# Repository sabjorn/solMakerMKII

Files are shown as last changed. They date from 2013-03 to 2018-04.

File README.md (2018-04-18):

## Sol(enoid)MakerMarkII
### About
Included in this package is all (I hope) the necessary components to build a copy of the Sol-MakerMKII solenoid control 'robot'.

This device was designed as a shield for an Arduino Uno R3 and you will, therefore, need to get one if you don't already have it. The circuit size (and cost) could be easily reduced by scaling the whole circuit to fit an Arduino Mini (the code should be cross compatible).

The basic principle of the device is this: electrical power is input into the device. This power is gated by twelve transistors which are closed. Each transistor is an output for a device which operates with applied electrical current (solenoids, for example). These transistor gates are controlled by the 12 digital output pins from the Ardunio Uno. By sending a signal to the Arduino, via the serial bus, the Arduino is able to open any/all of these transistor gates. Thus, if you attach a solenoid (electro-mechanical piston) to a gate, and open it with the Arduino, you can send electricity to the device and cause it to move.

Solenoids are not the only device for which this circuit will work. Anything which operated using a DC power supply (which matches the input voltage from your selected power supply) can be controlled. Example: Electric motors from tape machines.

**CAUTION**: This device will operate without issue if nothing is connected to the outputs. BUT if the outputs from the transistors are crossed, THE TRANSISTORS WILL BLOW UP. Furthermore, if the power supply voltage polarity is switched (+ and ground switched) THE TRANSISTORS WILL (also) BLOW UP. It would be a good idea to attach a diode to the power supply input to prevent this from happening by mistake.

The LEDs on this device act as indicators of the Arduino pins' activity. They will operate without the external power supply connected. They are helpful for troubleshooting connection problems and have the added benefit of looking very cool.
 
Included in this package:
	
	* Fritzing and Gerber file for PCB ('solMakerMKII_circuit' directory).

	* Code for the Arduino and a Max/MSP patch to allow direct use of MIDI 
	devices ('solMakerMKII_code' directory).

	* Diagrams ('solMakerMKII_diagrams' directory).
	
	* More elaborate documentation (.pdf file and the latex files needed to
	edit it; 'solMakerMKII_documentation' directory).

For contribution ideas, please check the .pdf documentation. There is a list at the end of the document. 

### Development Status
This project is effectively deprecated. The code will be ported to be used as part of another project--[dreamIO](https://github.com/sabjorn/dreamio). This will allow for control of solenoids over WiFi using OSC.

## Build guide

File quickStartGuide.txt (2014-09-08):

Quick Start Guide

1) Order PCB. The 'solMakerMKII_circuit' directory contains all the files for this. The Gerber directory contains the exported circuit (gerber files) created using Fritzing (open source PCB design software).

2) Assemble board. The 'solMakerMKII_diagrams' directory contains the specs for all the required components. A DC power supply will be required (voltage and maximum current will depend on the items being controlled by the circuit). Solenoids, or other DC powered items, will need to be found. The type of connectors used to attach the power supply and solenoids to the PCB will also be determened based on the context of the situationâ any type of connector you choose should work.

3) Flash the Arduino. The 'solMakerMKII_code' directory contains a directory called 'solMakerMKII' which houses the Arduino's code. The PCB is designed for an Arduino Uno and, with standard headers, should attach easily to the back of the board.

4) Open 'sol-MakerMKIIControl.maxpat'. This file is contained in the 'solMakerMKII_code' directory. It acts as a midi decoder. If you do not have Max/MSP, a free runtime can be download which will allow you to use the patch. Make sure the Arduino is connected, and recognized by your computer, via USB AND that no other task (i.e. Arduino serial window) is reading the Arduino's serial messages. Once the maxpatch is opened, the midi input can be changed to receive from any midi device or software (i.e. Ableton live). The Arduino code accepts midi notes 60 (C3) to 71 (B3) (inclusive) with standard velocity values when coupled with the maxpatch. If you have issue connecting to the Arduino with the patch, the Serial object may not be connecting to the right port.

5) Have fun.

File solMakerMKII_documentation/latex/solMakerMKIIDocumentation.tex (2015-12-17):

% $Id: AllegProposal.tex,v 1.8 2000/07/05 21:02:12 culver Exp $
% AllegProposal.tex
% by A. Thall
% 13. Feb 2003
%
% Small edits and a few additions made by R. Roos
% 21 Jan 2007
% Most particularly, the "box" around the thesis statement has been removed,
% section titles have been modified. The section named "Prior work II" has
% been commented out. The \topmargin has been changed to -.5in and the
% change to \parindent has been commented out.
% The filename "nausicaa.eps" has been changed to simply "nausicaa" so that
% pdflatex can be used on the file (and a file named "nausicaa.pdf" has
% been created using the "epstopdf" command).
% Several subsections have been added to illustrate subsection usage.
% The word "comp" has been replaced by "project" or "thesis" throughout.
% Other small changes have been made.
%
% This document provides a sample Senior Project Proposal template for use
% by students in Allegheny's CS and Applied Computing programs.

\NeedsTeXFormat{LaTeX2e}
\documentclass[12pt]{article}

%The following is used by WinEdt to set up cross-referencing to the BibTeX files
%It is NOT commented out---the comment lets it be simply ignored by non-WinEdt LaTeX compilers

%GATHER{mybibtexDB.bib}

\usepackage{setspace}
\usepackage{amsmath}
\usepackage{amssymb}
\usepackage{epsfig}
\usepackage{fancybox}
\usepackage{listings}
\usepackage{algo}
\usepackage{url}
\usepackage{hyperref}

% for watermakr
\usepackage{graphicx}
%\usepackage{tikz}
%\usepackage{eso-pic}

%\newcommand\BackgroundPicA{\put(-50,50){{
%\begin{tikzpicture}\node[opacity=0.15]{
%\includegraphics[scale=5.0]{test.png}};
%\end{tikzpicture}%
%}}}

%\makeatletter
%\AddToShipoutPicture{\BackgroundPicA}
%\makeatother

\setlength{\textheight}{9in}
\setlength{\textwidth}{6in}
\setlength{\oddsidemargin}{.25in}
\setlength{\topmargin}{-.5in}  % changed from -.25 by RSR on 1/21/07
%\parindent .5in    % commented out by RSR 1/21/07

%put words in the hyphenation statement if you want to enforce
%how LaTeX should break them (or not) at the end of a line.
%\hyphenation{repre-sen-tations problems exact linear}
\hyphenation{itself}

%%%%%
%% Commented out -- RSR, 1/21/07
%%%%%
% The following provides a box to surround the thesis statement
%\newenvironment{Thesis}%
%{\begin{Sbox}\begin{minipage}{.95\linewidth}}%
%{\end{minipage}\end{Sbox}\begin{center}\fbox{\TheSbox}\end{center}}

\title{Sol-MakerMKII: Arduino Uno Based Solenoid Controller}
\author{Steven A. Bj\o rnson}

\begin{document}

% You can specify a language and other options for
% the code-formatting "listings" package
\lstset{language=C++,basicstyle=\small,
        stringstyle=\ttfamily,showstringspaces=false}

\singlespace
\maketitle

\doublespace
% This sets section-numbering to only include Section and Subsection numbers
\setcounter{secnumdepth}{2}

\section{Outline:}\label{ch:overview}

The Sol-Maker MKII is a shield designed for the Arduino Uno. This shield allows for individual control of up to twelve solenoids (push, pull, or rotary) utilizing an external power supply; 12 or 24 volts depending on the power requirements of the solenoids. Control of each solenoid is made possible by communication with each of the 12 output pins on the Arduino UnoÐ1 pin per solenoid. The current code compiled on the Ardiuino allows the user to send messages on/off messages from a computer to the Arduino via the USB port.

\section{Circuit:}
The design of the circuit is quite simple. Each of the 12 digital outputs of the Arduino Uno (outputs 2 to 13) are connected to identical modules. Each module contains a resistor, a TIP120 transistor, and a diode. These modules allow the shared voltage (12 or 24 volt external power supply) to be controlled by the digital output of the Arduino for each solenoid.

	In each module the TIP120 acts as a gate which is opened and closed by the 5 volt output from the digital output pins of the Arduino. The resistor is necessary since the TIP120  provides very low impedance and so without it the Arduino could be damaged. 

		A diode is run in parallel with each solenoid. This is necessary because solenoids are inductors and after a solenoid is cycled (charged and released) the plunger returns to the starting point (by way of mechanical potential energy; a spring or gravity will return the plunger to home). This returning plunger pushes current the opposite direction in the circuit and thus without the diode this reversed current could potentially damage the transistor.

	The second section of each module contains a resistor and an light emitting diode (LED). This section is connected in parallel to each of the digital output pins which control the solenoids. When a solenoid is activated, a corresponding LED is activated. The LEDs are powered by the 5V provided by the digital outputs and do not utilize the external power supply. 

		A resistor in series with the LED provides the same function as the TIP120's resistor. 

		The purpose of the LED is to provide visual feedback and, since it will continue to operate when the external power supply is not on and when a solenoid is not connected, it notifies the user which module is being activated. This is advantageous for fault checking during system setup (i.e. finding out which output you are controlling before plugging a solenoid into that modules output).

\subsection{Solenoids:}
\begin{itemize}
\item Sol1 through Sol12 - GUARDIAN ELECTRIC TP6X12-I-24D 24V Solenoids.
\end{itemize}

Any solenoid with a voltage range of 12 to 24 volts should work with this circuit. There is a possibility of damaging a solenoid by holding current for too long if it is not designed to hold for long periods of time.\footnote{Remember that the input power supply voltage must match the requirement of your solenoids and that your power supply should have a maximum current rating to allow all the solenoids to fire at once. For example, since GUARDIAN ELECTRIC TP6X12-I-24D  solenoids require  24V and 198mA each, the power supply must produce 24V and be capable of producing a current of 2376mA.}

\subsection{Resistor Values:}
\begin{itemize}
\item R1 through R12 - 2.2 kOhm.
\item LED-R1 through LED-R12 - 100 Ohm.
\end{itemize}

\subsection{Diodes:}
\begin{itemize}
\item D1 through D12 - 1N4001 or other suitable diode.
\end{itemize}

\subsection{LEDs:}
\begin{itemize}
\item LED1 through LED12 - any colour; 5mm;\footnote{Resistors LED-R1 through LED-R12 are calculated based on 3.3Vf and 20mA. Thus, if an LED with a different Vf is used a change of it's corresponding resistor is required. The resistance of LED-R1 through LED-R12 was set higher than required in the hopes of preventing any issue problem when using different colour LEDs.}
\end{itemize}

\section{Control:}
Control is possible utilizing the USB port on the Arduino. The code (outline below) allows the user to send an on/off byte to each solenoid individually by coupling the byte with an address. Thus, although Max/MSP has been utilized for control, any programming language or software can be used as long as it follows serial message format.

\section{Dynamics:}
Originally \emph{pulse width modulation} (PWM) was used for all supported pins with the belief that control of the output voltage would be useful for the dynamic capability of the solenoids. This was unfortunate because the Arduino Uno only supports 6 pins for PWM. It became apparent, however, that PWM was unnecessary since the velocity of the solenoids can be effectively controlled with the hold-time--the length of time that current is pushed through a solenoid. Thus, if a solenoid is given current for 10ms it will hit with less force than if current is held for 20ms. Each solenoid is likely to have idiosyncrasies and thus a method of calibration would be useful\footnote{A microphone is likely a requirement for such an operation. I.e.  A microphone would have to be placed near the device and it's sound energy output measured at various stages (5ms, 10ms, 20ms, etc). Once the sound energy hit it's maximum (maximum dB), the maximum current holding value is found. Each solenoid would have to undergo this process and it would depend greatly on the distance from the object being struck. If the solenoid was to be moved in any way, it would likely have to be re-calibrated. Furthermore, this calibration process could be used to create a table for midi value scaling. Nonetheless, this can all be done by ear, although not with optimum effect} but a simple scaling of MIDI velocity (0 - 127) with a range of 5 - 100ms should suffice.

\section{Future Improvements:}
\begin{itemize}
\item A multiplexer could be used to increase number of solenoids. An alternative would be to use an 	Arduino Mega which supports a larger number of digital output pins. 
\item Since the shield obscures the Arduino completely a serial send/receive light on the board would be useful.
\item  With an Arduino network adapter shield the system could easily utilize Open Sound Control (OSC) making the whole system more user friendly. Otherwise a simple MIDI input port would be sufficient for greater usability.
\item To reduce the cost of manufacturing, the circuit could be redesigned to fit an Arduino Mini.
\item To prevent accidentally plugging the power supply in with the polarity reversed, the circuit could be redesigned to include a diode at the power input. 
\end{itemize}

\end{document}

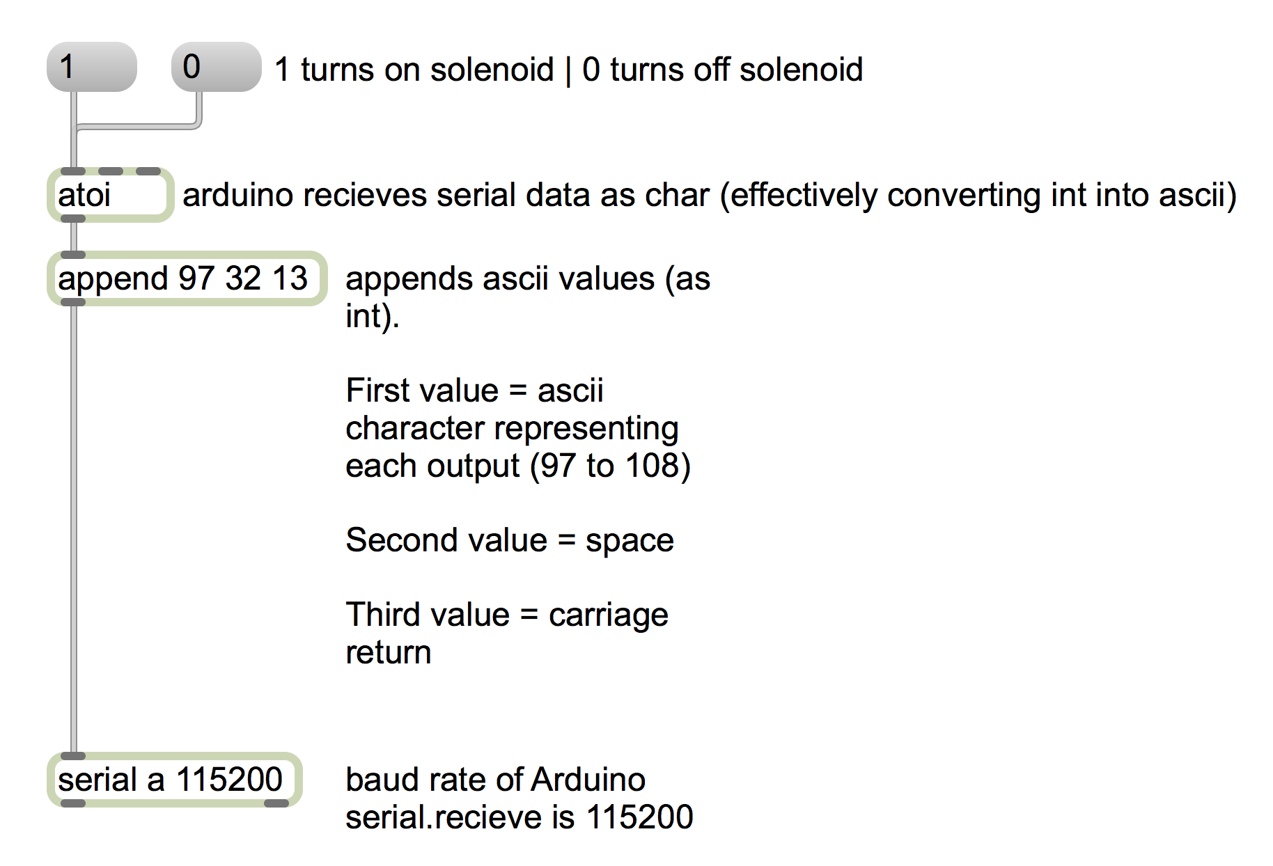
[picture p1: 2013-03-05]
solMakerMKII_documentation/images/sol-makerSimpleExample.png

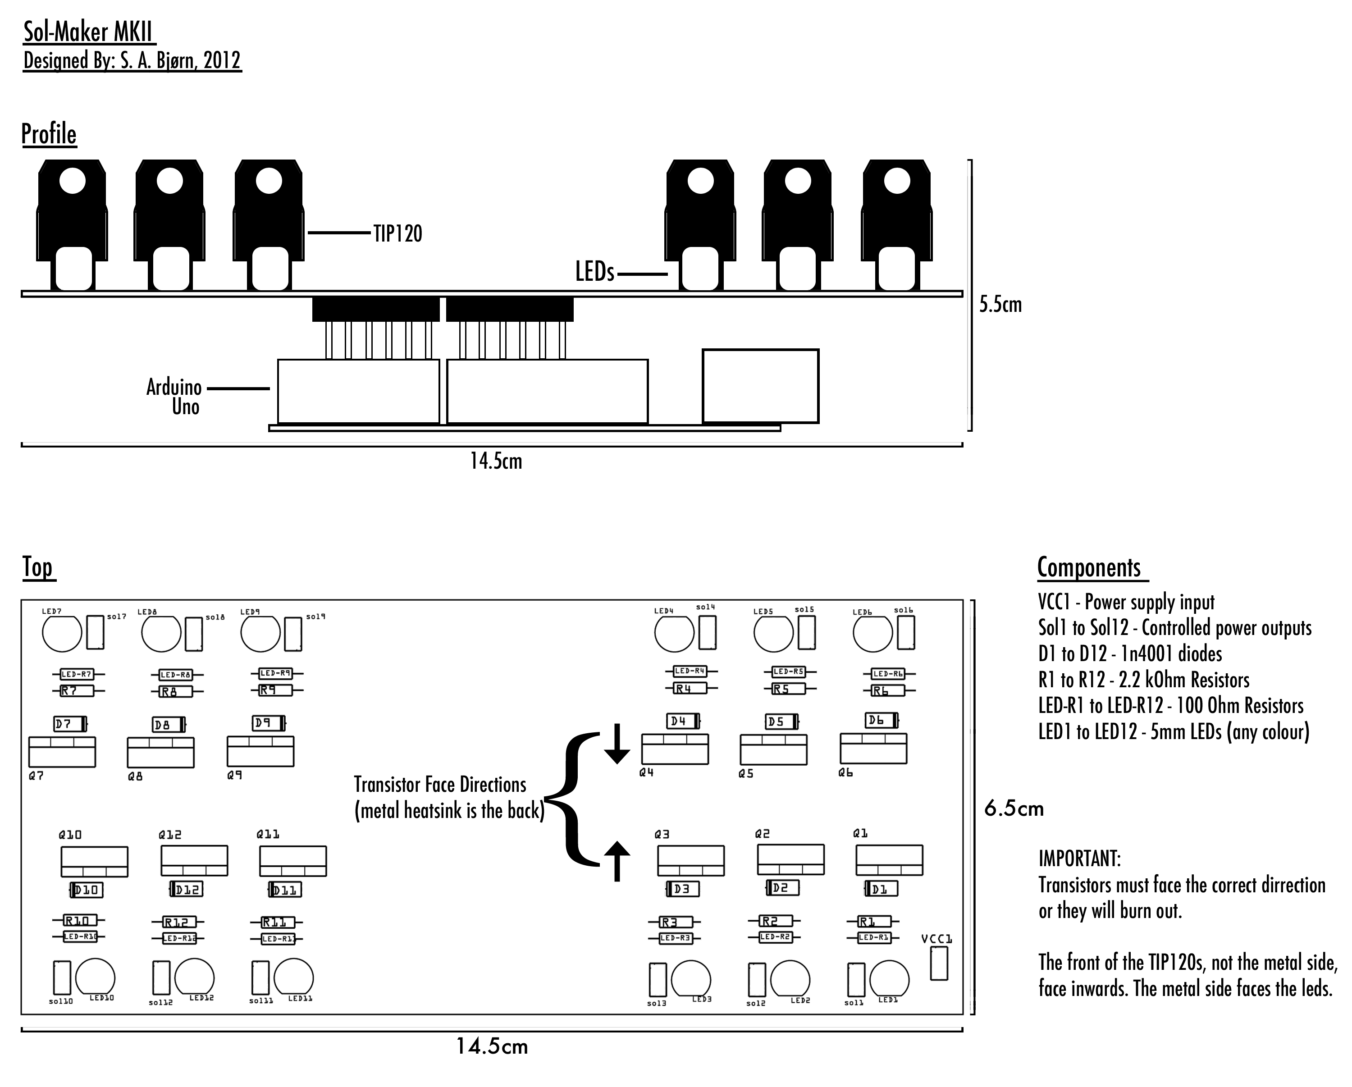
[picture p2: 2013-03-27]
solMakerMKII_diagrams/solMakerMKII-diagram.png

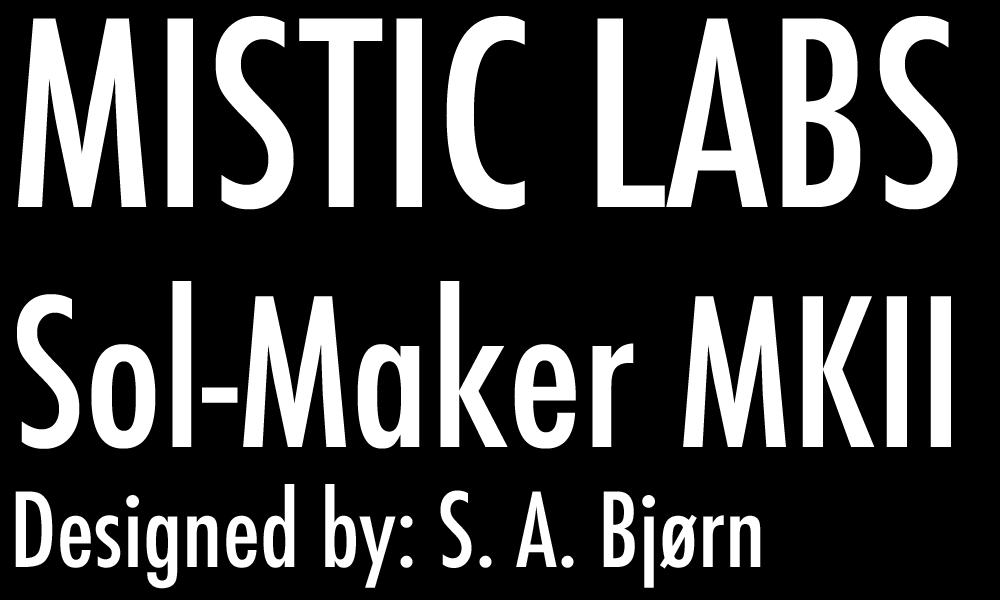
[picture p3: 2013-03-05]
solMakerMKII_circuit/fritzing/mistic2.gif

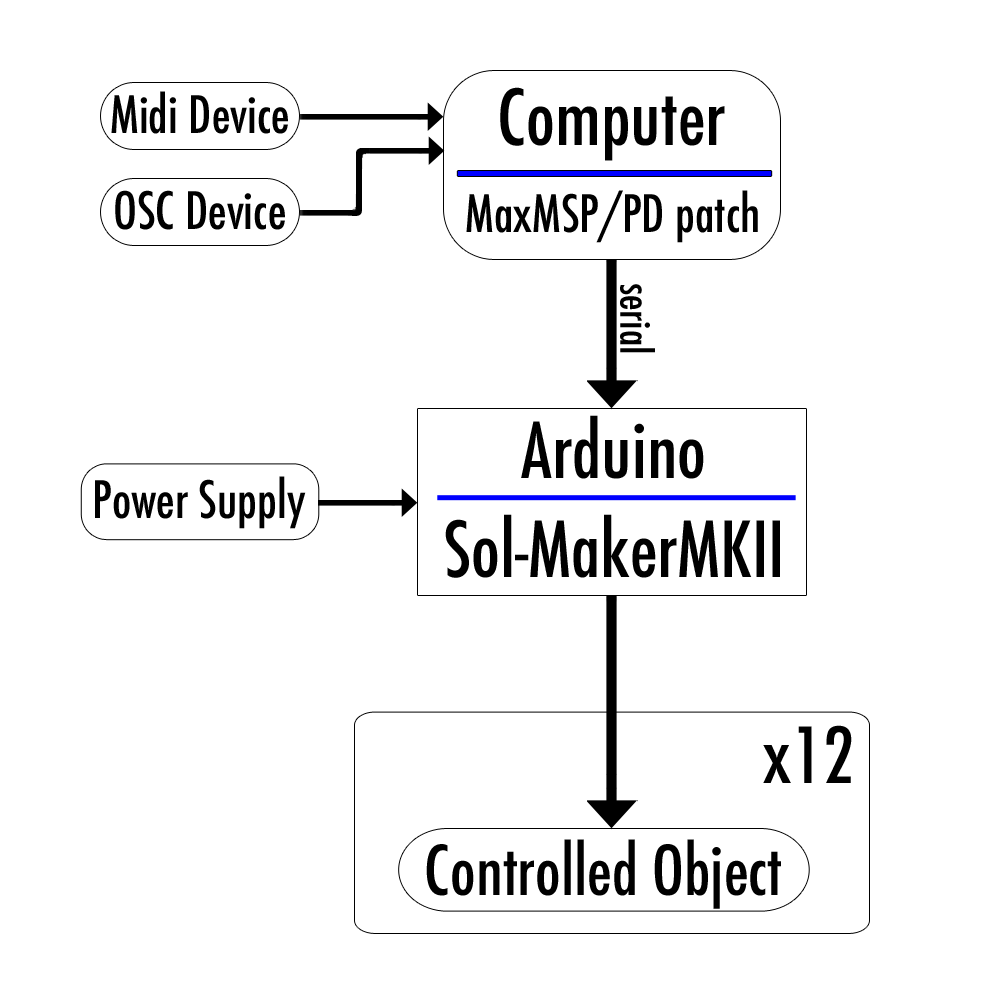
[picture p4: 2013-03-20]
solMakerMKII_diagrams/solMakerMKII-systemDiagram.png

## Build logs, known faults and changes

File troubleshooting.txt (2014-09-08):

Troubleshooting Guide:

LEDs:
The circuit is designed so that even if there is no external power, the Arduino's power will still light up the LEDs when it receives a valid message. The circuit was designed like this to enable the user to quickly troubleshoot problems.

If LEDs do not operate, check to make sure that the serial receive ('rx') light is operating on the Arduino when a signal is sent via USB. If no message is being sent, try changing the serial port in the solMakerMKIIMidiControl.maxpat (patch can be edited using text editor. The Serial object is set to port 'a', try ports 'b', 'c', etc). If the Arduino software serial monitor window is open, the maxpatch will not work.

If the Arduino's serial receive light is operating there may be a problem with the connection between the Arduino and the board or there may be issues with the soldering, or the installation, of components (specifically LED-R1 through LED-R12 and LED1 through LED12).

Not Current Output:

If the LEDs are working and there is no current coming out of the board (sol1 through sol12) then the power supply connection should be checked first. If the power supply is connected properly and operating normally, the TIP120 transistors may be wired backwards (although this is not likely the case because a revered current will usually cause the transistors to burn out) or may not have a solid connection. The resistors attached to the TIP120s (R1 through R12) may also have poor connections. 

It is unclear what may happen if the diodes (D1 through D12) are connected backwards. The TIP120 transistors are likely to be damaged.

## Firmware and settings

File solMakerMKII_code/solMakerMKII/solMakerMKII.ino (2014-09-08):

/*
solMakerMKII
Copyright September 2014, Steven A. Bjornson

Based on code by Chris Vecchio, 2010 (http://www.noisemantra.com/Physical%20Computing/arduino-MaxMSP%20communications%2011.pdf).

Distributed under the terms of the GNU General Public License.

This file is part of SolMakerMKII, an open source solenoid control system.

SolMakerMII is free software (and hardware): you can redistribute it and/or modify it under the terms of the GNU General Public License as published by the Free Software Foundation, either version 3 of the License, or (at your option) any later version.

SolMakerMKII is distributed in the hope that it will be useful, but WITHOUT ANY WARRANTY; without even the implied warranty of MERCHANTABILITY or FITNESS FOR A PARTICULAR PURPOSE.  

See the GNU General Public License for more details.

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
This code will allow user to send data to Arduino over USB to active 12 of the digital output pins. 
When connected to the solMakerMKII board, these 12 outputs will control the flow of an external power supply in order to turn ON and OFF solenoids.
*/

// used to set the OFF state of arduino pin output register
uint8_t out_mask[8] = 
{
	B00000001,
	B00000010,
	B00000100,
	B00001000,
	B00010000,
	B00100000,
	B01000000,
	B10000000
};
// used to set the OFF state of arduino pin output register
uint8_t out_mask_clear[8] = 
{
	B11111110,
	B11111101,
	B11111011,
	B11110111,
	B11101111,
	B11011111,
	B10111111,
	B01111111
};

unsigned long current; // location to store current time (ms)

uint8_t check_serial = 0; // serialEvent() function (runs when serial message exists) and turns this flag HIGH if new message.

char buffer[40]; // used to store Serial data.
uint8_t index = 0; // used by Serial.read to keep track of buffer[] location.

// a data structure to keep track of information for each output.
struct sol
{
  uint8_t ascii; // stores channel code for output (range is 'a' through 'l')
  uint16_t velocity; // amount of time output is held HIGH (ms)
  long oldtime; // used to keep track of when the output was turned on.
};

// array of sol struct objects, one for each output.
struct sol solenoids[12];

void setup() {
	Serial.begin(115200);

	for(int n = 0; n < 12; n++) // fills struct arrays.
  	{
    	solenoids[n].ascii = n+97;
    	solenoids[n].velocity, solenoids[n].oldtime = 0;
  	}

  	// set GPIO resgisters to output
    DDRD = B11111111;
    DDRB = B11111111;

}

void loop() {
	uint8_t tempB, tempD = B00000000; // place to store temp register values

	for(int i = 0; i < 12; i++)
	{
		current = millis();
		if(long(solenoids[i].velocity) > (current - solenoids[i].oldtime)) //turn output on if the amount of time that is is supposed to be on has not completed
		{
			// 'port manipulation' is used instead of digitalWrite() because it is 50 - 100 times faster.
			if(i < 6)
			{
				tempD = tempD | out_mask[i+2];
			}
			else
			{
				tempB = tempB | out_mask[(i+2)%8];
			}
		}
		else // turn outputs off if enough time has elapsed (velocity vs. current time - time when outputs recieved ON message)
		{
			if(i < 6)
			{
				tempD = tempD & out_mask_clear[i+2];
			}
			else
			{
				tempB = tempB & out_mask_clear[(i+2)%8];
			}			
			solenoids[i].velocity = 0;
		}
	}

	// change state of GPIOs
	PORTB = tempB;
	PORTD = tempD;

	// if check_serial flag is high, get data from Serial.
	if(check_serial)
	{
		current = millis();

		index = 0;
		do
		{
			buffer[index] = Serial.read();  // get a byte from the serial port
			if (buffer[index]!=-1)
			{
				index = index+1;    // -1 if no byte is present
			}
			else if (buffer[index-1] == solenoids[0].ascii) // checks for ASCII code 'a'
			{
			  	solenoids[0].velocity = check_length(atoi(buffer)); // if 'a' convert input to int
			  	solenoids[0].oldtime = current;
			}
			else if (buffer[index-1] == solenoids[1].ascii) // checks for ASCII code 'b'
			{
			  	solenoids[1].velocity = check_length(atoi(buffer)); // if 'b' convert input to int
			  	solenoids[1].oldtime = current;
			}
			else if (buffer[index-1] == solenoids[2].ascii) // checks for ASCII code 'c'
			{
			  	solenoids[2].velocity = check_length(atoi(buffer)); // if 'c' convert input to int
			  	solenoids[2].oldtime = current;
			}
			else if (buffer[index-1] == solenoids[3].ascii) // checks for ASCII code 'd'
			{
			  	solenoids[3].velocity = check_length(atoi(buffer)); // if 'd' convert input to int
			  	solenoids[3].oldtime = current;
			}
			else if (buffer[index-1] == solenoids[4].ascii) // checks for ASCII code 'e'
			{
			  	solenoids[4].velocity = check_length(atoi(buffer)); // if 'e' convert input to int
			  	solenoids[4].oldtime = current;
			}
			else if (buffer[index-1] == solenoids[5].ascii) // checks for ASCII code 'f'
			{
			  	solenoids[5].velocity = check_length(atoi(buffer)); // if 'f' convert input to int
			  	solenoids[5].oldtime = current;
			}
			else if (buffer[index-1] == solenoids[6].ascii) // checks for ASCII code 'g'
			{
			  	solenoids[6].velocity = check_length(atoi(buffer)); // if 'g' convert input to int
			  	solenoids[6].oldtime = current;
			}
			else if (buffer[index-1] == solenoids[7].ascii) // checks for ASCII code 'h'
			{
			  	solenoids[7].velocity = check_length(atoi(buffer)); // if 'h' convert input to int
			  	solenoids[7].oldtime = current;
			}
			else if (buffer[index-1] == solenoids[8].ascii) // checks for ASCII code 'i'
			{
			  	solenoids[8].velocity = check_length(atoi(buffer)); // if 'i' convert input to int
			  	solenoids[8].oldtime = current;
			}
			else if (buffer[index-1] == solenoids[9].ascii) // checks for ASCII code 'j'
			{
			  	solenoids[9].velocity = check_length(atoi(buffer)); // if 'j' convert input to int
			  	solenoids[9].oldtime = current;
			}
			else if (buffer[index-1] == solenoids[10].ascii) // checks for ASCII code 'k'
			{
			  	solenoids[10].velocity = check_length(atoi(buffer)); // if 'k' convert input to int
			  	solenoids[10].oldtime = current;
			}
			else if (buffer[index-1] == solenoids[11].ascii) // checks for ASCII code 'l'
			{
			  	solenoids[11].velocity = check_length(atoi(buffer)); // if 'l' convert input to int
			  	solenoids[11].oldtime = current;
			}
		} while (buffer[index-1] != 13);
		check_serial = 0;
	}

}

void serialEvent()
{
	// Set check_serial flag high if Serial message recieved
	check_serial = 1;
}

// makes sure 'velocity' does not go past 30,000ms (prevent solenoid burnout)
uint16_t check_length(int input)
{
	if(input < 30000)
	{
		return input;
	}
	else
		return 30000;
}

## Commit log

2013-03-27 -Simplified Arduino code, expanded documentation, and extended usability of maxpatch.
    [solMakerMKII.fzz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]
2013-03-28 removed accidently added files.
    [solMakerMKII.fzz, solenoidControl.fzz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]
2014-09-08 Timing ported to Arduino (messages now include ms 'velocity') Created a Python example scipt for controlling Arduino
2014-09-08 Added reset and mute button to Max/Msp midi patch.
2014-09-08 minor edits for grammar to .txt files changed .maxpatch to display current input MIDI note.
2014-09-09 changed default values for velocity in Max/MSP control file.
